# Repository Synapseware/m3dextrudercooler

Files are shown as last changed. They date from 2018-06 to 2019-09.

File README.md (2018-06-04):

M3D Pro and Micro Extruder Cooler
=================================

## About
The M3D Pro (and micro to some extent) suffer from some really terrible design decisions.  For example, after printer for about 15-20 minutes on the Pro, the extruder usually heats up enough to melt the filament, which of course causes the print to fail and the extruder gear to get all jammed up with melted filament.

This cooler aims to solve that by monitoring the temperature at or near the extruder gear and directing a fan to blow more or less depending on how hot it is.

# MCU
The controlling chip is an ATTiny25/45/85 running around 8MHz and driven from a 5V supply (using a USB-wall wort, LM7805, etc.).

## ADC Input
The cooler samples the ADC input every 10 seconds or so, and ramps up fan speed based on temperature.

### ADC Input Pin
The ADC is configured to read from pin PB3.

### ADC Sense Line
The input to the ADC should be constrained to 0.0v through 1.1v.  This gives the most accuracy on the ADC and allows for a small load/sense resistor.

## PWM Output
Timer1 is used to generate the PWM signal that drives the MOSFET which is connected to the motor.  The switching frequency is set for best performance with the given fan, and will need to be tuned in firmware.

### PWM Output Pin
The PWM output is available on PB1.  The output should not be filtered since it must be fed to the MOSFET switch.  Care should be taken to keep this line short and include an appropriately sized pull-down resistor to ensure safe operation of the power MOSFET or other switching transistor.

## Other Chip Information
The AVR uC is configured to use it's internal R/C oscillator.  High clock accuracy is not needed by this circuit and keeping the part count low is a goal of this example.

## Build
This project compiles and uploads just fine using Linux and avr-gnu.

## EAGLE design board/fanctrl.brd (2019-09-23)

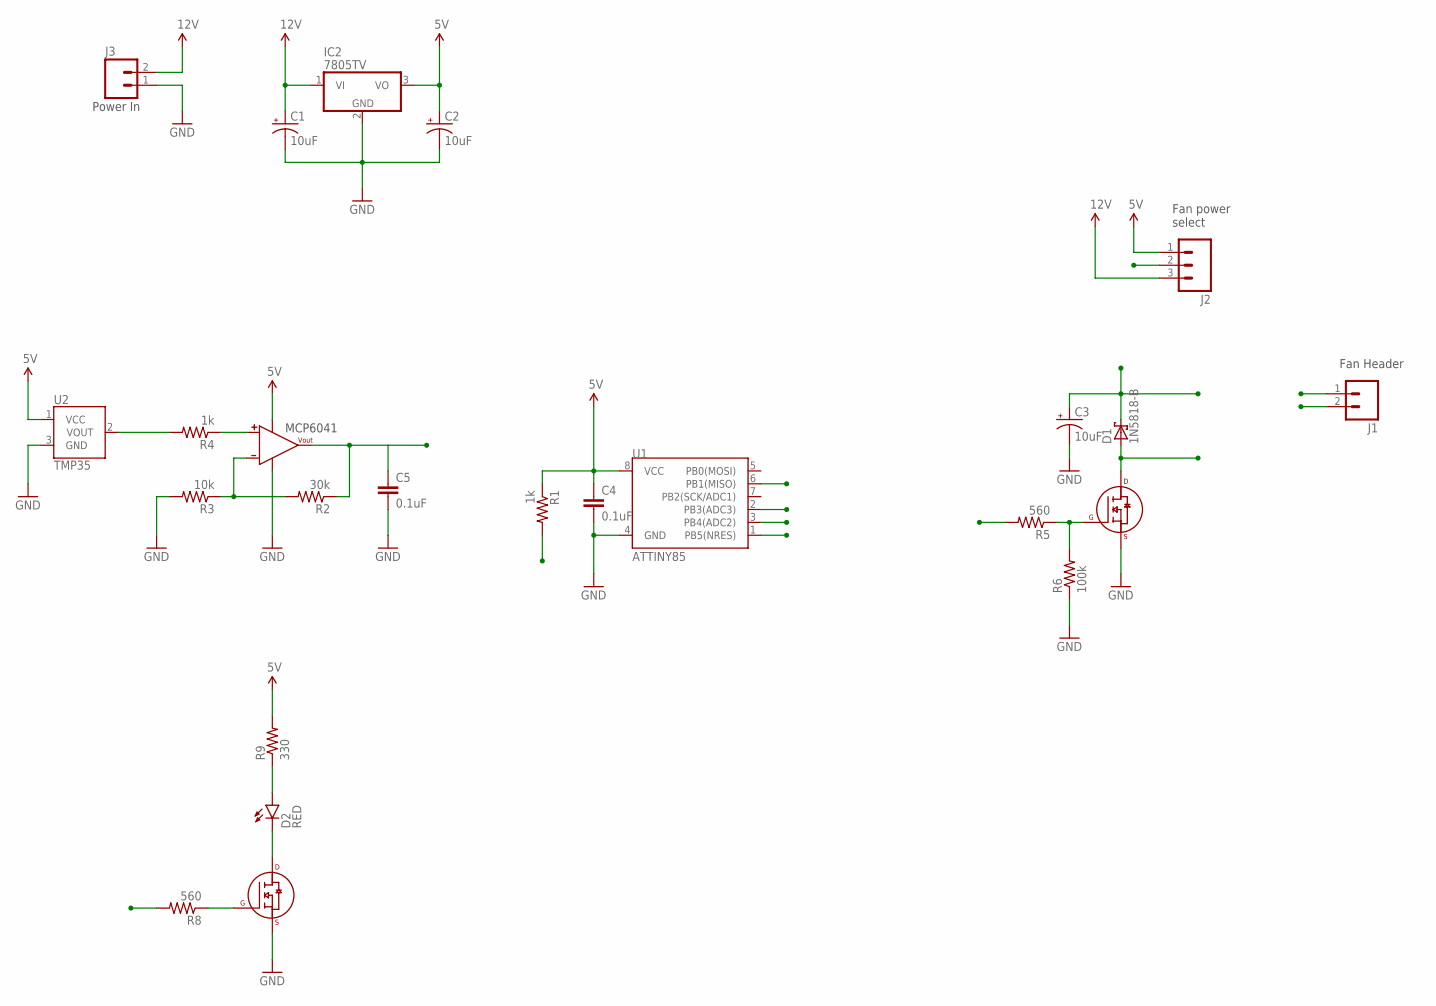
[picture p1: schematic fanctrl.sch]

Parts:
C1, C2, C3: 10uF; CPOL-RADIAL-10UF-25V
C4, C5: 0.1uF; CAP-PTH-SMALLEZ
D1: 1N5818-B; DO41-7.6
D2: RED; LED5MM
IC2: 7805TV; TO220V
J1: M02JST-PTH-VERT; JST-2-PTH-VERT
J2: M03PTH; 1X03
J3: M02PTH; 1X02
MCP6041: MCP6041DIP; PDIP-8
R1, R4: 1k; AXIAL-0.1
R2: 30k; AXIAL-0.1
R3: 10k; AXIAL-0.1
R5, R8: 560; AXIAL-0.1
R6: 100k; AXIAL-0.1
R9: 330; AXIAL-0.1
U1: ATTINY85; DIP08
U2: TMP35; TO-92
U$1, U$2: 2N7000; TO-92

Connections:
5V: C2.1 (+), C4.1, IC2.3 (VO), J2.1, MCP6041.7 (VDD), R1.P$1 (1), R9.P$2 (2), U1.8 (VCC), U2.1 (VCC)
12V: C1.1 (+), IC2.1 (VI), J2.3, J3.2
/RESET: R1.P$2 (2), U1.1 (PB5(NRES))
FAN_POWER: C3.1 (+), D1.C, J1.1, J2.2
GND: C1.2 (-), C2.2 (-), C3.2 (-), C4.2, C5.2, IC2.2 (GND), J3.1, MCP6041.4 (VSS), R3.P$2 (2), R6.P$1 (1), U1.4 (GND), U2.3 (GND), U$1.3 (S), U$2.3 (S)
LED: R8.P$2 (2), U1.3 (PB4(ADC2))
MOTOR-: D1.A, J1.2, U$1.1 (D)
unnamed: R4.P$2 (2), U2.2 (VOUT)
unnamed: MCP6041.2 (-), R2.P$2 (2), R3.P$1 (1)
unnamed: R5.P$1 (1), R6.P$2 (2), U$1.2 (G)
unnamed: MCP6041.3 (+), R4.P$1 (1)
unnamed: D2.A, R9.P$1 (1)
unnamed: D2.K (C), U$2.1 (D)
unnamed: R8.P$1 (1), U$2.2 (G)
PWM: R5.P$2 (2), U1.6 (PB1(MISO))
SENSOR: C5.1, MCP6041.6 (VOUT), R2.P$1 (1), U1.2 (PB3(ADC3))

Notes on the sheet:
MCP6041
Fan power select
Power In
Fan Header

Board: 2 copper layers, 24 parts (0 on the bottom side), 16 nets, no tracks yet.

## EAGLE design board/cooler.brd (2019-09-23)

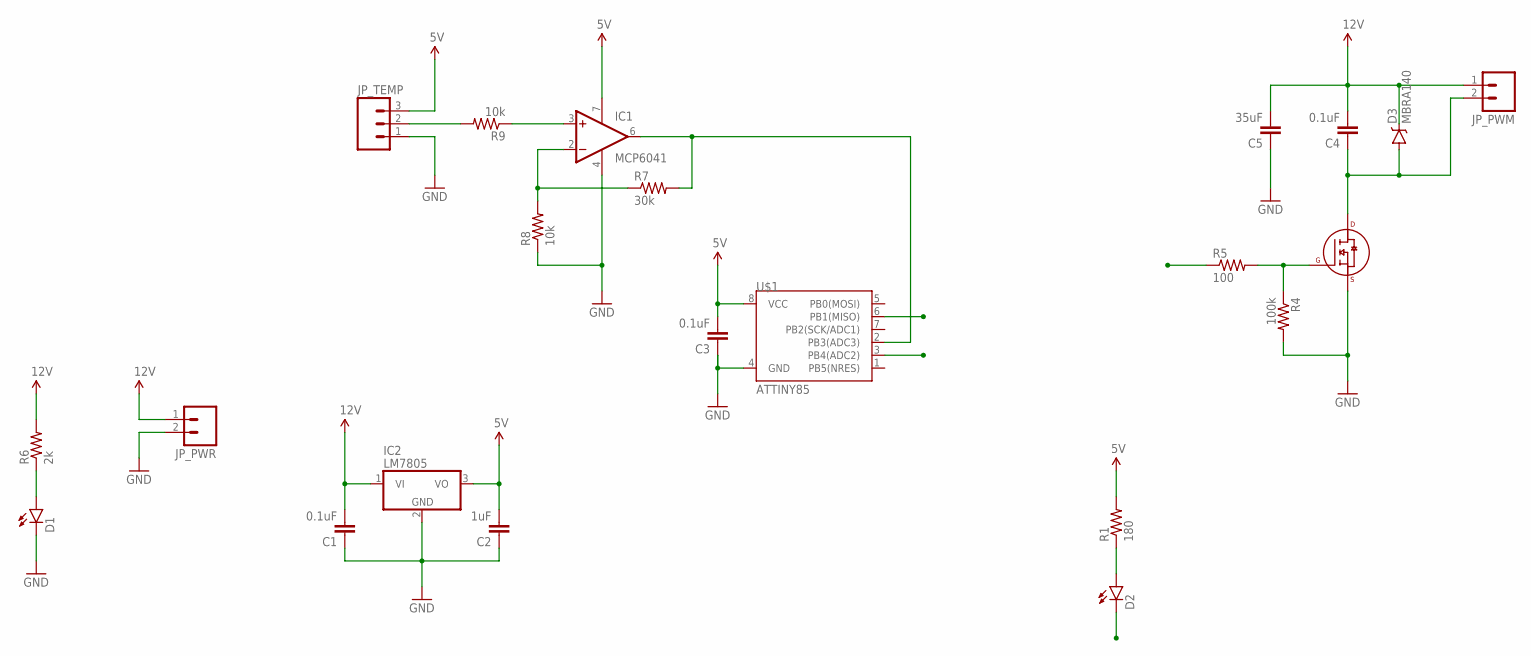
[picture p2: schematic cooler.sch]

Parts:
C1, C3, C4: 0.1uF; 1210
C2: 1uF; 1210
C5: 35uF; 1210
D1, D2: LED1206; LED-1206
D3: MBRA140; SMA-DIODE
IC1: MCP6041; SO08
IC2: LM7805; TO220V
JP_PWM: M02LOCK_LONGPADS; 1X02_LOCK_LONGPADS
JP_PWR: M02LOCK_LONGPADS; 1X02_LOCK_LONGPADS
JP_TEMP: M03LONGPADS; 1X03_LONGPADS
Q2: 2N7000-2SOT-23; SOT-23-3
R1: 180; R2010
R4: 100k; R2010
R5: 100; R2010
R6: 2k; R2010
R7: 30k; R2010
R8, R9: 10k; R2010
U$1: ATTINY85; SO08

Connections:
5V: C2.2, C3.2, IC1.7 (V+), IC2.3 (VO), JP_TEMP.3, R1.2, U$1.8 (VCC)
12V: C1.2, C4.2, C5.2, D3.C, IC2.1 (VI), JP_PWM.1, JP_PWR.1, R6.2
ADC_IN: IC1.6 (OUT), R7.2, U$1.2 (PB3(ADC3))
GND: C1.1, C2.1, C3.1, C5.1, D1.C, IC1.4 (V-), IC2.2 (GND), JP_PWR.2, JP_TEMP.1, Q2.2 (S), R4.2, R8.1, U$1.4 (GND)
LED: D2.C, U$1.3 (PB4(ADC2))
unnamed: Q2.1 (G), R4.1, R5.2
unnamed: D1.A, R6.1
unnamed: IC1.3 (+IN), R9.1
unnamed: IC1.2 (-IN), R7.1, R8.2
unnamed: D2.A, R1.1
unnamed: C4.1, D3.A, JP_PWM.2, Q2.3 (D)
PWM: R5.1, U$1.6 (PB1(MISO))
TMP_IN: JP_TEMP.2, R9.2

Board: 2 copper layers, 22 parts (0 on the bottom side), 13 nets, no tracks yet.

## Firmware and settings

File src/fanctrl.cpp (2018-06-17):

#include "fanctrl.h"
#include "board.h"

volatile uint8_t	tFast		= 0;
volatile uint8_t	tSeconds	= 0;
volatile int	 	adcData		= 0;
volatile uint8_t	state		= 0;

Events events(8);

//----------------------------------------------------------------
// 
static void init(void)
{
	// disable interrupts
	cli();

	// set defaults
	GTCCR		= 0;
	TIMSK		= 0;
	TIFR		= 0;
	DDRB		= 0;
	PORTB		= 0;
	DIDR0		= 0;
	tFast		= 0;
	tSeconds	= 0;
	adcData		= 0;
	state		= STATE_INIT;

	// setup hardware
	ConfigureSystemTimer();
	ConfigurePWMOutputTimer();
	ConfigureADC(ADC_CHANNEL);
	ConfigureDebugLed();

	// enable interrupts
	sei();
}


//----------------------------------------------------------------
// Flags the ADC to start a conversion
static void StartConversion(eventState_t state)
{
	// start an ADC conversion
	ADCSRA |= (1<<ADSC);
}


//----------------------------------------------------------------
// Smooths the ADC sample by averaging readings
static void ProcessADCValue(int sample)
{
	// basic moving average
	adcData = (sample>>2) + adcData - (adcData>>2);
}


//----------------------------------------------------------------
// 
static int GetLatestAdcData(void)
{
	// just return the ADC data
	return adcData;
}


//----------------------------------------------------------------
// Converts the value from the temperature sensor to degrees C
static uint8_t ConvertToCelcius(int sample)
{
	// Temperature sensor is a TMP35

	// ADC transfer function:
	// ADC value = (Vin * 1024) / Vref
	//			Vin * 1024
	// sample = ----------   or,
	//			   5.0v
	// 
	// Vin = 5.0v/1024
	//
	// TMP35 temperature range is 10-125/C
	// 		Output voltage is 0.10 - 1.25
	//		Output calibrated directly in degrees C
	//
	// The board has an op-amp which essentially multiplies the
	// output from the TMP35 by 4.  So, full voltage range being
	// input to the ADC is 0.4v to 5.0v
	//
	// TMP35 transfer function is 5.0/125, or 40mV/C (0.04V/C)
	//
	// To convert from an ADC sample to a temperature (Tc), we need:
	//
	// Tc = (sample * 5.0v/1024) / (5.0v / 125C)
	//
	// Constant portion of the ADC to temp. transfer function is about
	// 0.12207
	// Ex1: sample = 712: Temp = (712)(0.12207) => 86.9 => 86C
	// Ex2: sample = 454: Temp = (454)(0.12207) => 55.4 => 54C

	// An easier solution, is this transfer function:
	//			(ADCresult)(Vref)
	// Ftemp = ------------------(25)
	//				1024
	//
	//return (uint8_t) ((sample * (5.0/1024.0)) / (5.0 / 125.0));

	return (uint8_t) (sample * (5.0/1024.0) * 25);
}


//----------------------------------------------------------------
// Maps the temperature to a fan speed (between 0-100)
// 49 & less = 0%
// 50 - 99 = 50% to 100%
// 100 & more = 100%
static uint8_t MapFanSpeed(uint8_t temperature)
{
	// The motor is off at temperatures below 50/C and on at
	// 100% for all speeds from 100/C and up.
	// For 50/C to 99/C, the fan speed is controlled by a parabolic
	// curve.
	// The parabolic speed curve for the motor temps is defined by 
	// a parabola having vertex (50,153) and a point of (100,255).
	// y=a(x-h)^2+k
	// (h,k) = (50,153)
	// (x,y) = (100,255)
	// a = 102/2500 => 0.0408
	// y= 0.0408(x-50)^2+153

	uint8_t map = 0;
	if (temperature < 50)
	{
		// turn the fan off for all temps below 50/C
		map = 0;
	}
	else if (temperature < 100)
	{
		// map the temperature to fan speed
		map = 0.0408 * pow(temperature - 50, 2) + 153;
	}
	else
	{
		// max
		map = 255;
	}

	return map;
}


//----------------------------------------------------------------
// Sets the PWM duty cycle based on desired fan speed %
static void SetFanSpeed(uint8_t speed)
{
	// This needs to convert a speed percentage to a workable
	// duty cycle for the fan.  Typically, this is somewhere
	// between 60% - 100%
	// The speed is provided as some value between 50% and 100%
	if (speed > 0)
	{
		DDRB |= (1<<PWM_OUTPUT);
		PWM_REG = speed;
	}
	else
	{
		DDRB &= ~(1<<PWM_OUTPUT);
	}
}


//----------------------------------------------------------------
// Sets the current processing state
static void SetState(uint8_t whatState)
{
	// set the state
	state = whatState;
}


//----------------------------------------------------------------
// Gets the current processing state
static uint8_t GetState(void)
{
	// return the state
	return state;
}


//----------------------------------------------------------------
// Processes the statemachine which responds to temperature changes
static void ProcessStateMachine(eventState_t state)
{
	static int decay			= 0;
	static uint8_t lastTemp		= 0;

	//PINB |= (1<<LED_DBG);

	// read the current temperature and map it to a fan speed
	uint8_t currentTemp = ConvertToCelcius(GetLatestAdcData());
	uint8_t speed = MapFanSpeed(currentTemp);

	switch (GetState())
	{
		case STATE_INIT:
			SetFanSpeed(100);
			decay = 5;
			lastTemp = currentTemp;
			SetState(STATE_DECAY);
			break;

		case STATE_HOT:
			decay = 30;
			SetFanSpeed(speed);
			SetState(STATE_HOT_NXT);
			break;

		case STATE_HOT_NXT:
			// current temp has to keep dropping until the decay is 0
			if (decay > 0)
			{
				if (currentTemp < lastTemp)
				{
					// hold speed here
					decay--;
				}
				else
				{
					// let the fan speed increase
					SetFanSpeed(speed);
					decay = 30;
				}

				decay--;
			}
			else
			{
				SetState(STATE_NEXT);
			}
			break;

		case STATE_COOL:
			// just set the fan speed and allow the system to throttle
			// down as necessary
			SetFanSpeed(speed);
			SetState(STATE_NEXT);
			break;

		case STATE_DECAY:
			if (--decay > 0)
				break;
			SetState(STATE_NEXT);
			break;

		case STATE_NEXT:
			// figure out if the current level of cooling is enough
			if (currentTemp > lastTemp + 3)
			{
				SetState(STATE_HOT);
			}
			else
			{
				SetState(STATE_COOL);
			}

			// save the current temp
			lastTemp = currentTemp;

			break;
	}
}


//----------------------------------------------------------------
// 
static void ledOn(eventState_t state)
{
	PORTB |= (1<<LED_DBG);
}
static void ledOff(eventState_t state)
{
	PORTB &= ~(1<<LED_DBG);
}


//----------------------------------------------------------------
// 
int main(void)
{
    // let the Events instance know what the period size is
    events.setTimeBase(1000);

    // Register a function to toggle an I/O pin to turn an LED on and off
    events.registerEvent(ProcessStateMachine, 1000, EVENT_STATE_NONE);
    events.registerEvent(StartConversion, 100, EVENT_STATE_NONE);
    events.registerEvent(ledOn, 1000, EVENT_STATE_NONE);
    events.registerEvent(ledOff, 1100, EVENT_STATE_NONE);

	init();

	while(1)
	{
		// handle events
		events.doEvents();
	}

	return 0;
}


//----------------------------------------------------------------
// ADC interrupt complete handler
ISR(ADC_vect)
{
	// just read the ADCH register (top 8 bits)
	ProcessADCValue(ADC);
}


//----------------------------------------------------------------
// Timer 0 compare A interrupt handler @ 100Hz
ISR(TIMER0_COMPA_vect)
{
    events.sync();
}

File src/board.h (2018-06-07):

#ifndef __BOARD_H__
#define __BOARD_H__


#include <avr/io.h>
#include <avr/interrupt.h>
#include <inttypes.h>
#include <avr/sleep.h>
#include <avr/power.h>
#include <util/delay.h>



void ConfigureSystemTimer(void);
void ConfigurePWMOutputTimer(void);
void ConfigureADC(uint8_t channel);
void SelectADCChannel(uint8_t channel);
void ConfigureDebugLed(void);




//--------------------------------------------------
// Board constants
#define	ADC_CHANNEL		3
#define ADC_SMOOTHING	4
#define LED_DBG			PB4
#define PWM_OUTPUT		PB1
#define PWM_REG			OCR1A
#define PWM_TOP			OCR1C




//-----------------------------------------------------------------------------
// ADC values
// ADMUX
#define ADC_VREF_VCC	0
#define ADC_VREF_EXT	((0<<REFS2) | (0<<REFS1) | (1<<REFS0))
#define ADC_VREF_INT11	((0<<REFS2) | (1<<REFS1) | (0<<REFS0))
#define ADC_VREF_256	((1<<REFS2) | (1<<REFS1) | (0<<REFS0))
#define ADC_VREF_256BP	((1<<REFS2) | (1<<REFS1) | (1<<REFS0))
#define ADC_LEFTADJ		((1<<ADLAR))
#define ADC_RIGHTADJ	0
#define ADC_CHANNEL_0	((0<<MUX3) | (0<MUX2) | (0<<MUX1) | (0<<MUX0))
#define ADC_CHANNEL_1	((0<<MUX3) | (0<MUX2) | (0<<MUX1) | (1<<MUX0))
#define ADC_CHANNEL_2	((0<<MUX3) | (0<MUX2) | (1<<MUX1) | (0<<MUX0))
#define ADC_CHANNEL_3	((0<<MUX3) | (0<MUX2) | (1<<MUX1) | (1<<MUX0))
#define ADC_CHANNEL_BGP	((1<<MUX3) | (1<MUX2) | (0<<MUX1) | (0<<MUX0))
#define ADC_CHANNEL_GND	((1<<MUX3) | (1<MUX2) | (0<<MUX1) | (1<<MUX0))
#define ADC_CHANNEL_TMP	((1<<MUX3) | (1<MUX2) | (1<<MUX1) | (1<<MUX0))

// ADCSRA
#define ADC_ENABLE		(1<<ADEN)
#define ADC_NO_INTS		0
#define ADC_INT_EN		(1<<ADIE)
#define ADC_AUTOTRG		(1<<ADATE)
#define ADC_CLK_1		((0<<ADPS2) | (0<<ADPS1) | (0<<ADPS0))
#define ADC_CLK_2		((0<<ADPS2) | (0<<ADPS1) | (1<<ADPS0))
#define ADC_CLK_4		((0<<ADPS2) | (1<<ADPS1) | (0<<ADPS0))
#define ADC_CLK_8		((0<<ADPS2) | (1<<ADPS1) | (1<<ADPS0))
#define ADC_CLK_16		((1<<ADPS2) | (0<<ADPS1) | (0<<ADPS0))
#define ADC_CLK_32		((1<<ADPS2) | (0<<ADPS1) | (1<<ADPS0))
#define ADC_CLK_64		((1<<ADPS2) | (1<<ADPS1) | (0<<ADPS0))
#define ADC_CLK_128		((1<<ADPS2) | (1<<ADPS1) | (1<<ADPS0))

// ADCSRB
#define ADC_BIN			((1<<BIN))
#define ADC_IPR			((1<<IPR))
#define ADC_TRG_FREE	((0<<ADTS2) | (0<<ADTS1) | (0<<ADTS0))
#define ADC_TRG_COMP	((0<<ADTS2) | (0<<ADTS1) | (1<<ADTS0))
#define ADC_TRG_EI0		((0<<ADTS2) | (1<<ADTS1) | (0<<ADTS0))
#define ADC_TRG_TC0A	((0<<ADTS2) | (1<<ADTS1) | (1<<ADTS0))
#define ADC_TRG_TC0F	((1<<ADTS2) | (0<<ADTS1) | (0<<ADTS0))
#define ADC_TRG_TC0B	((1<<ADTS2) | (0<<ADTS1) | (1<<ADTS0))
#define ADC_TRG_PCIR	((1<<ADTS2) | (1<<ADTS1) | (0<<ADTS0))


//-----------------------------------------------------------------------------
// Timer0
// GTCCR
#define TC0_SYNC		((1<<TSM))
#define TC0_PSR			((1<<PSR0))

// TCCR0A
#define TC0_OUTA_NRM	((0<<COM0A1) | (0<<COM0A0))
#define TC0_OUTA_TGL	((0<<COM0A1) | (1<<COM0A0))
#define TC0_OUTA_CLR	((1<<COM0A1) | (0<<COM0A0))
#define TC0_OUTA_SET	((1<<COM0A1) | (1<<COM0A0))
#define TC0_OUTB_NRM	((0<<COM0B1) | (0<<COM0B0))
#define TC0_OUTB_TGL	((0<<COM0B1) | (1<<COM0B0))
#define TC0_OUTB_CLR	((1<<COM0B1) | (0<<COM0B0))
#define TC0_OUTB_SET	((1<<COM0B1) | (1<<COM0B0))

// TCCR0B
#define TC0_CLK_OFF		((0<<CS02) | (0<<CS01) | (0<<CS00))
#define TC0_CLK_1		((0<<CS02) | (0<<CS01) | (1<<CS00))
#define TC0_CLK_8		((0<<CS02) | (1<<CS01) | (0<<CS00))
#define TC0_CLK_64		((0<<CS02) | (1<<CS01) | (1<<CS00))
#define TC0_CLK_256		((1<<CS02) | (0<<CS01) | (0<<CS00))
#define TC0_CLK_1024	((1<<CS02) | (0<<CS01) | (1<<CS00))
#define TC0_CLK_EXTFAL	((1<<CS02) | (1<<CS01) | (0<<CS00))
#define TC0_CLK_EXTRIS	((1<<CS02) | (1<<CS01) | (1<<CS00))

// TIMSK
#define TC0_IE_COMPA	((1<<OCIE0A))
#define TC0_IE_COMPB	((1<<OCIE0B))
#define TC0_IE_OVFLW	((1<<TOIE0))


//-----------------------------------------------------------------------------
// Timer1
// GTCCR
#define TC1_PWM1B		((1<<PWM1B))
#define TC1_PSR			((1<<PSR1))
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

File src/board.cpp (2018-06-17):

#include "board.h"


//----------------------------------------------------------------
// Configures Timer0 for 1kHz interrupt
void ConfigureSystemTimer(void)
{
	// For 25kHz output
	// 8MHz / 64 / 125 = 1000Hz

	TCCR0A	=	(1<<WGM01)	|	// CTC
				(0<<WGM00);

	TCCR0B	=	(0<<WGM02)	|	// CTC
				TC0_CLK_64;

	TIMSK	|=	TC0_IE_COMPA;		// Compare A interrupts

	OCR0A	=	125-1;				// Set for 1kHz
	OCR0B	=	64;
}


//----------------------------------------------------------------
// Configures Timer1 for PWM output (25kHz)
void ConfigurePWMOutputTimer(void)
{
	// 8Mhz / 8 / 40 = 25kHz
	TCCR1	=	TC1_PWM1A	|	// Enable PWM Channel A
				(1<<COM1A1)	|	// OC1A set on match
				(0<<COM1A0)	|	// /OC1A disconnected
				TC1_CLK_1;		// CLK/1

	// Setup PLLCSR - note: PLL is enabled via fuses because we are driving uC clock from the PLL! (pg 97)
	PLLCSR	=	0;

	PWM_REG	=	153;			// Set default PWM duty cycle
	PWM_TOP	=	255;			// PWM range

	DDRB	|=	(1<<PWM_OUTPUT);	// Enable PWM output
}


//----------------------------------------------------------------
// Setup ADC to read from the temp sensor.
void ConfigureADC(uint8_t channel)
{
	ADMUX	=	ADC_RIGHTADJ|	// Right adjust result
				ADC_VREF_VCC;	// Vcc as Aref

	ADCSRA	=	ADC_ENABLE	|	// ADC Enable
				ADC_INT_EN	|	// Enable interrupts
				ADC_CLK_128;	// Fcpu/128

	ADCSRB	=	0;				// Nothing to set here

	SelectADCChannel(channel);
}


//----------------------------------------------------------------
// Selects the specified ADC channel
void SelectADCChannel(uint8_t channel)
{
	switch (channel)
	{
		case 0x00:
			// Channel 0
			ADMUX = (ADMUX & 0xF0) | (0<<MUX3) | (0<MUX2) | (0<<MUX1) | (0<<MUX0);
			DIDR0 = (1<<ADC0D);
			DDRB &= ~(1<<PB5);
			break;
		case 0x01:
			// Channel 1
			ADMUX = (ADMUX & 0xF0) | (0<<MUX3) | (0<MUX2) | (0<<MUX1) | (1<<MUX0);
			DIDR0 = (1<<ADC1D);
			DDRB &= ~(1<<PB2);
			break;
		case 0x02:
			// Channel 2
			ADMUX = (ADMUX & 0xF0) | (0<<MUX3) | (0<MUX2) | (1<<MUX1) | (0<<MUX0);
			DIDR0 = (1<<ADC2D);
			DDRB &= ~(1<<PB4);
			break;
		case 0x03:
			// Channel 3
			ADMUX = (ADMUX & 0xF0) | (0<<MUX3) | (0<MUX2) | (1<<MUX1) | (1<<MUX0);
			DIDR0 = (1<<ADC3D);
			DDRB &= ~(1<<PB3);
			break;
		case 0x0C:
			// Band-gap voltage
			ADMUX = (ADMUX & 0xF0) | (1<<MUX3) | (1<MUX2) | (0<<MUX1) | (0<<MUX0);
			break;
		case 0x0D:
			// Ground
			ADMUX = (ADMUX & 0xF0) | (1<<MUX3) | (1<MUX2) | (0<<MUX1) | (1<<MUX0);
			break;
		case 0x0F:
			// Internal temperature sensor
			ADMUX = (ADMUX & 0xF0) | (1<<MUX3) | (1<MUX2) | (1<<MUX1) | (1<<MUX0);
			break;
	}
}


//----------------------------------------------------------------
// Configure Debug LED
void ConfigureDebugLed(void)
{
	DDRB |= (1<<LED_DBG);
	PORTB &= ~(1<<LED_DBG);
}

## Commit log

2018-06-04 Initial state machine processing
    Smartly run the fans by forcing a cool-down period, after which the fan
    can speed up, but not speed down until the temp of the extruder starts
    to fall.
2018-06-07 Use board file for hardware config
2018-06-07 Timers working, motor control non-functional
2018-06-17 Use a parabolic function for fan speed
2018-07-29 Added circuit schematic
    [fanctrl.brd, fanctrl.sch]
2019-09-23 Cooler control board
    [cooler.brd, cooler.sch]

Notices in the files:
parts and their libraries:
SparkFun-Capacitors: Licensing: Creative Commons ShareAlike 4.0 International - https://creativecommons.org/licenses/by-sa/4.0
